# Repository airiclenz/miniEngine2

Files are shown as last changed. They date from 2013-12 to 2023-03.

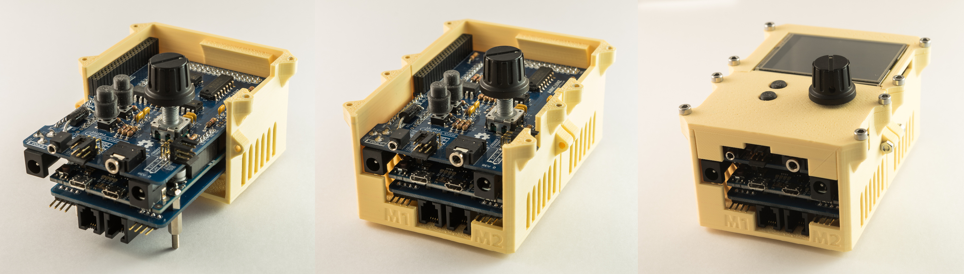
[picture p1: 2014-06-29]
Enclosures/3D Printing/Airic Lenz/miniE_case_assembly_steps.jpg

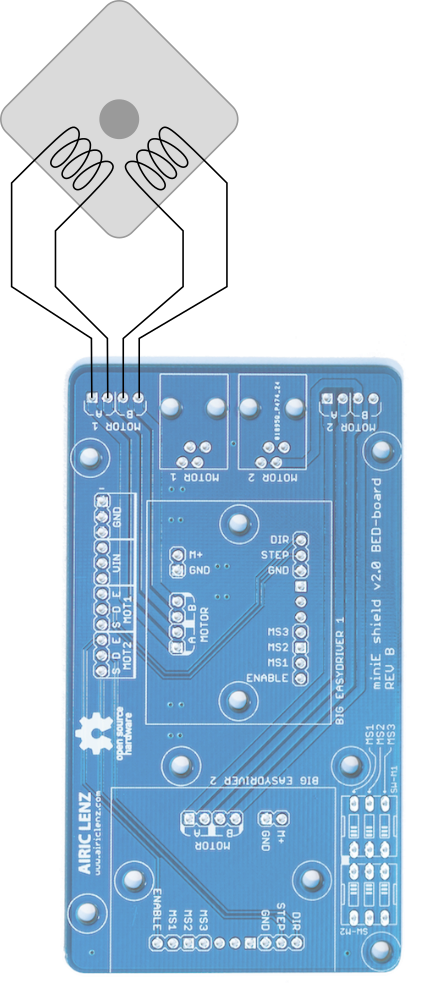
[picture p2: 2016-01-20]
Documentation/steppermotor connection.png

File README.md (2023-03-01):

miniEngine 2
============

An Arduino based multi-axis-motion-control system for time-lapse and video photogtaphy.

This repository contains all that is needed to build a full miniEngine 2 system. It contains:

	- Software
	- Hardware (PCB Gerber files)
	- Documentation
	- Licenses

Note of thanks
--------------

Four of the six contained software libraries were developed by me but two were not:

The library UTFT (here in version 2.0) was developed by Henning Karlsen
http://henningkarlsen.com/electronics/library.php?id=52

The DueTimer library was developed by Ivan Seidel 
https://github.com/ivanseidel/DueTimer

A big „Thank you“ to both of you for making these libraries available!

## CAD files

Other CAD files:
Enclosures/3D Printing/Airic Lenz/miniE2_Case.skp

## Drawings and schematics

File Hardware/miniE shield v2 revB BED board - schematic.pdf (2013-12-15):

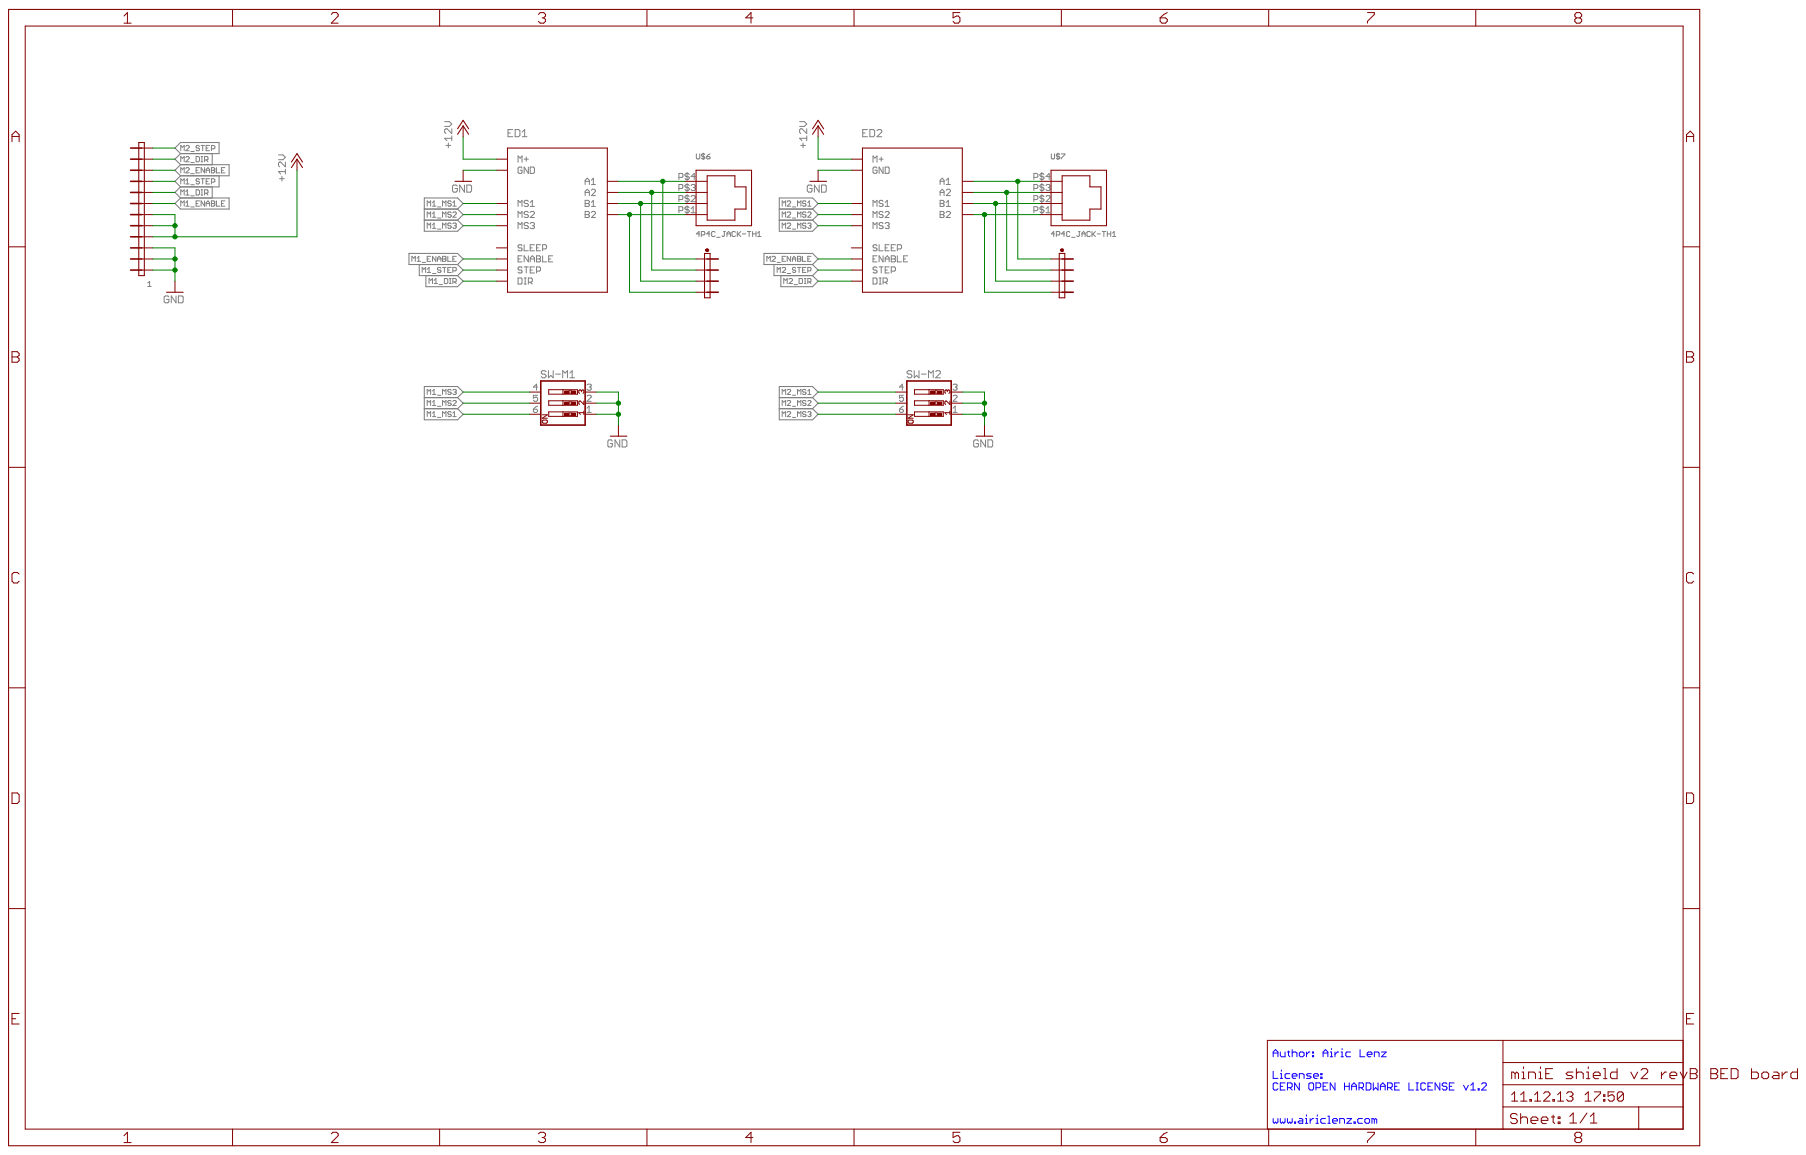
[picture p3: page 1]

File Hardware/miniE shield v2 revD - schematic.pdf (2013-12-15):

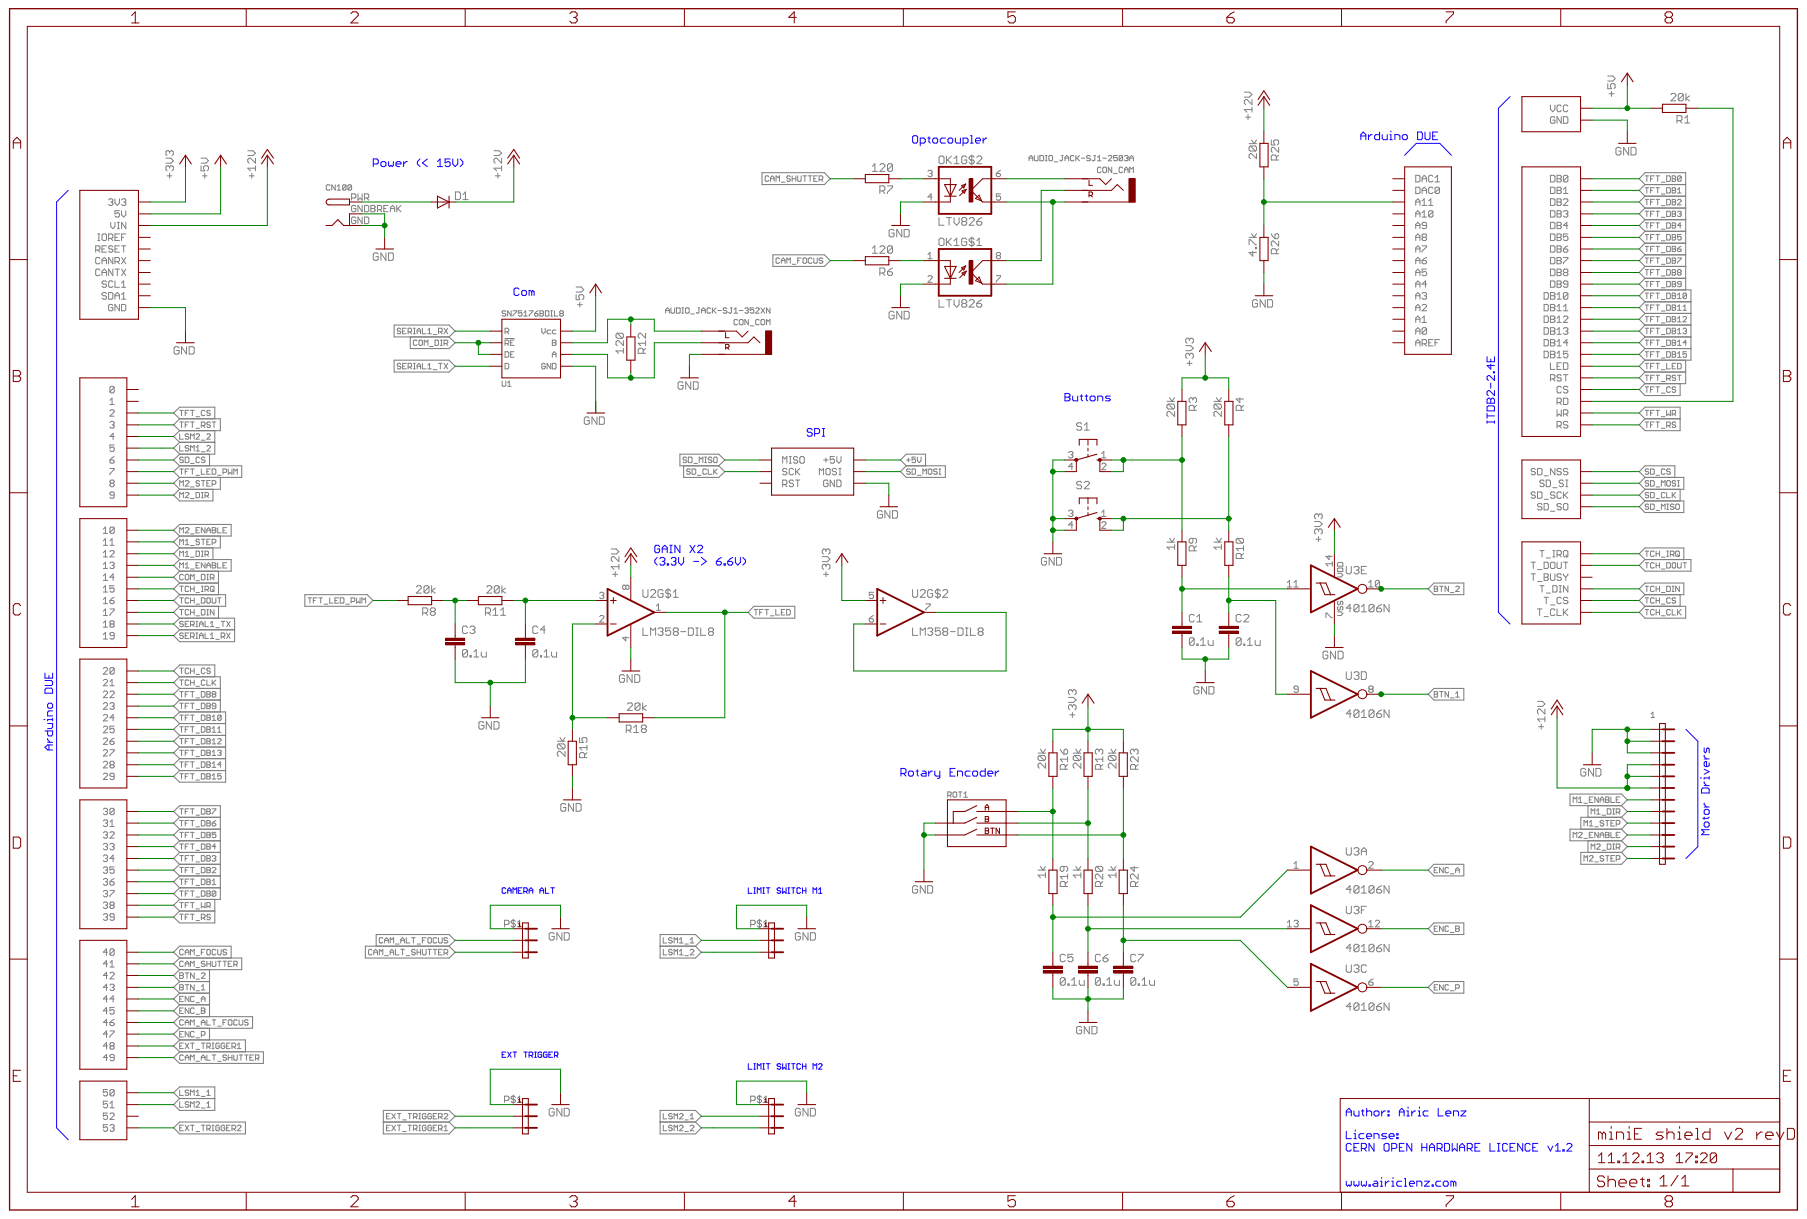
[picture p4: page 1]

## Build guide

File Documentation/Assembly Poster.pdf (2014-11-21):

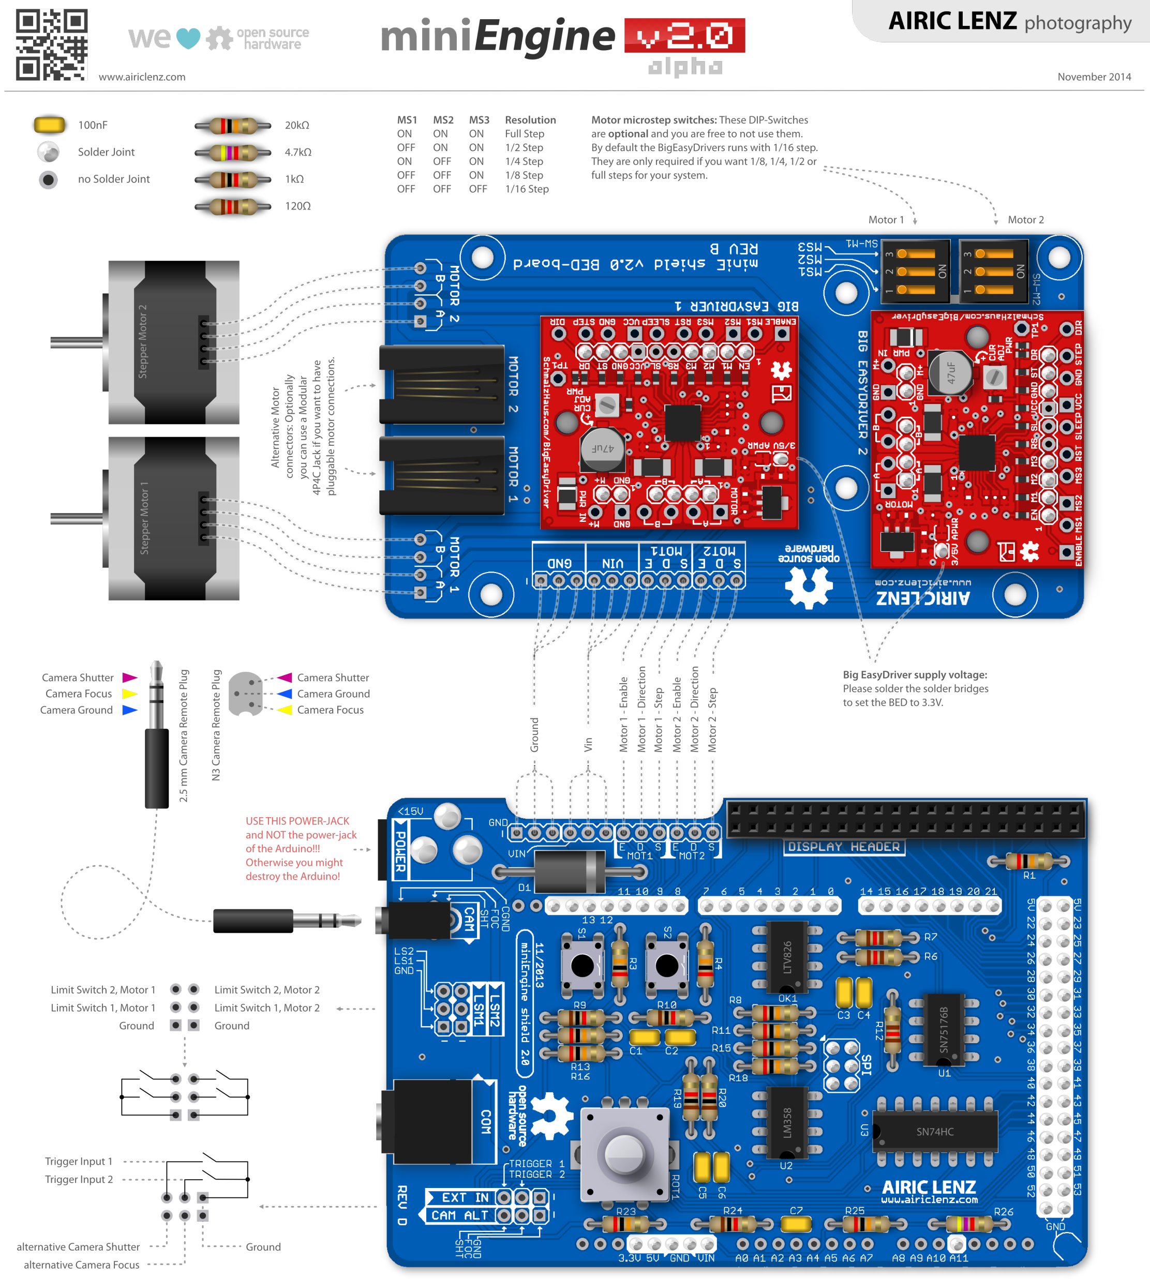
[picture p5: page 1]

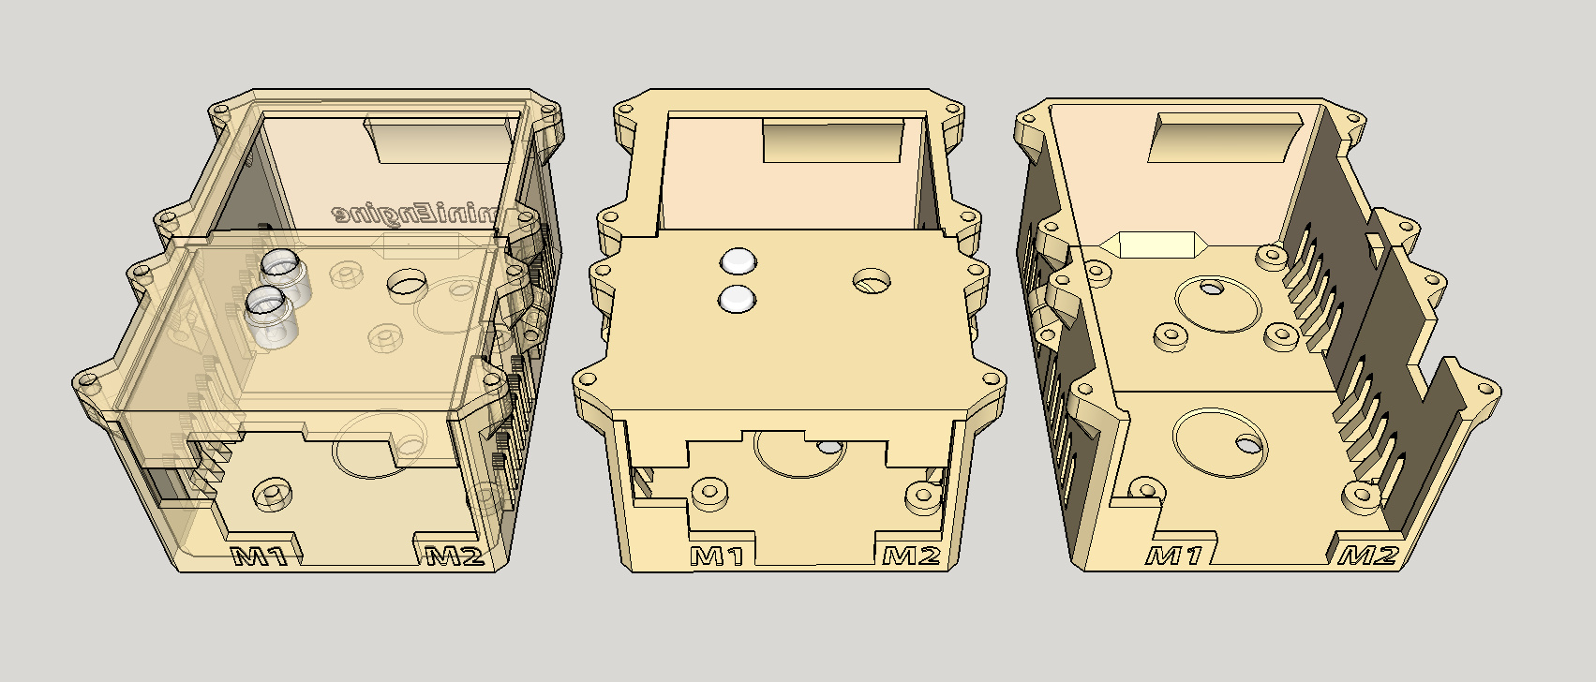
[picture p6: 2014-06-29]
Enclosures/3D Printing/Airic Lenz/miniE_case_3D.jpg

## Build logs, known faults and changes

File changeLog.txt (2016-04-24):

/////////////////////////////////////////////////////
version:	2.0.8
date:		2016-04-20

Software:

-	Added a feature to allow the camera to continue shooting
	even after the program run has ended until the user aborts
	(in Timelapse Mode)
-	Added a feature to delay the start of the motors after the
	program was started.
-	Fixed some bugs

/////////////////////////////////////////////////////
version:	2.0 alpha 7
date:		2015-07-29

Software:

-	Bouncing functionality which allows to loop the moves in 
	Video mode.
-	Multiple Language support. You can now add your own 
	language to the system. German is already included in this update.
	This feature was indroduced by Sascha Henke.
-	Added Camera Focus feature to allow a separate focus phase 
	before the exposure phase.
-	Fixed a bug that caused prevented correct saving of the 
	settings to the SD card.
-	Basic Daisy-Chaining functionality is already included but 
	not all features are in there yet.

/////////////////////////////////////////////////////
version:	2.0 alpha 6
date:		2014-06-29

Software:

-	fixed a bug that causes the initial move in SMS move to be
	wrong
-	fixed a bug in the painting routines that sometimes caused
	memory overflows
-	fixed some bugs in the core motor routines that under some conditions
	caused instable behaviour
-	added core functions for analyzing a curves max speed
-	added warning and abort if the motor-max-speed for a started
	action exceeds the defined limits
-	activating the pop-up menu now also on a menu-button long-press
-	added new pop-up menu functionalities:
	*	Set start > Defines the new start position for a move
		(equals "set home for all motors". This updates move-distance
		as well as move direction)
	*	Set End: Defines the new end position for a move
		(updates move-distance as well as move direction)
	*	Preview: Runs the timelapse setup with real-speed (total 
		preview duration = playback time) to get a feeling for the 
		planned moves. 
-	changed edit-granularity for the option "record time" 
	to 1 second for all values below 1 minute
- 	changed the FPS setting to be settable to any value between
	1 and 255
-	optimized code for ad-hoc curve generation (e.g. one move in
	SMS; move to home) for smoother moves and more consistent 
	behaviour
-	Increased Uplink functionality (for new minEngine Studio features)

Enclosures:

	- added enclosures to the resporitory

/////////////////////////////////////////////////////
version:	2.0 alpha 5
date:		2014-05-19

Documentation:

-	added a detailed assembly description for the BED
	Boards

Software:

-	added connectivity to the minEngine Studio software
	*	added new "Keyframes Mode" which is dedicated to work 
		only together with the miniEngine Studio
-	added a function that updates settings to the new version
	(no settings get lost during an update)
-	improved dashboards
-	improved settings menu-header
-	optimized system modes and run styles for easier use
-	fixed a bug where the motor was not moving when
	motor sleep was enabled
-	fixed a bug that not saved the keep powered status

/////////////////////////////////////////////////////
version:	2.0 alpha 4
date:		2014-02-19

Software:

-	added external trigger input system (starting, stopping 
	and shooting the camera)
-	added a Dashboards that is displayed when the miniEngine 
	is running
-	added a messaging system
-	added a new system font

/////////////////////////////////////////////////////
version:	2.0 alpha 3
date:		2014-01-25

Documentation:

-	updated the documentation (added small system-user-manual)
-	added some information about updating the software

Software:

-	fixed a bug which started moves from the wrong position 
	if not moved to home before
-	fixed a bug that moved the motor in the wrong direction
	when using the function "Move home (all)"
-	fixed a bug which cause the motor direction to change 
	sporadically during motor jogging
-	added a new menu font and a fon option
-	Minor user interface changes
-	added all needed libraries into the repository

/////////////////////////////////////////////////////
version:	2.0 alpha 2
date:		2013-12-18

Software:

- 	improved in-system help	to multiline text
-	fixed a motor-direction-bug in SMS mode 

/////////////////////////////////////////////////////
version:	2.0 alpha 1
date:		2013-12-17

Documentation:

-	added a motor-jack warning
- 	corrected an error with a wrong resistor-color-code 

Software:

-	added motor home functions to the pop-up menu
-	added action-menu-point functionalities
- 	implemented an intital simple help system 

/////////////////////////////////////////////////////
version:	2.0 alpha 0
date:		2013-12-15

- initial realease of the miniEngine v2 (still in alpha)

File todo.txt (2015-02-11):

TODO For v2 alpha 7
===================

-	daisy chaining
-	bouncing
-	language
-	focus time

TODO New Functionalities / IDEAS
================================

- 	check limit switch sensitivity
- 	add "Bouncing" functionality
- 	make keyframes from the minEngine Studio savable on the miniEngine
- 	add "About" screen
-   bulb ramping
-   park position for transport
-   names for axes (instead of motor 1, motor 2, ...)
-   changable limit switch retract amount
-   all axes joystick
-   panorama mode

TODO Bugs
=========

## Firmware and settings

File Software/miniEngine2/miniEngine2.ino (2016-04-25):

/*

    Author: Airic Lenz, C.A. Church
    Year of release: 2016
    
    See www.airiclenz.com for more information

    The 1st version of this code, dealing with core functionalities, 
    was heavily inspired by the OpenMoCo Engine by C.A. Church
    and is basically based on it. Thank you for your great work! 
        
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
*/


#ifdef __arm__
  #include "itoa.h"
#endif

#include <SPI.h>
#include <SD.h>

#include <UTFT.h>
#include <RotaryEncoder.h>
#include <StepperMotor.h>
#include <MoCoM.h>
#include <bitOps.h>
#include <DueTimer.h>

// free mem stuff
#include <malloc.h>
#include <stdlib.h>
#include <stdio.h>

extern char _end;
extern "C" char *sbrk(int i);
char *ramstart=(char *)0x20070000;
char *ramend=(char *)0x20088000;



// some replacements for fast coding
//#define   prn   Serial.print
//#define   prnl  Serial.println



////////////////////////////////////////////////////////
//                                                    //
//  L A N G U A G E                                   //
//                                                    //
////////////////////////////////////////////////////////

#define LANGUANGE_ENGLISH
//#define LANGUANGE_GERMAN
//#define LANGUANGE_ITALIAN


////////////////////////////////////////////////////////
//                                                    //
//  D I S P L A Y   T Y P E                           //
//                                                    //
////////////////////////////////////////////////////////


// if you have an older version of the display, use
// this line of code (if you get a white screen with
// this one, change to the other display type):
#define DISPLAY_TYPE        ITDB24E_16    

// if you have a newer version of the display or you get a
// white screen, use one of these lines of code 
// (remove the "//" and add it to the above definition):

//#define DISPLAY_TYPE        TFT01_24_16
//#define DISPLAY_TYPE        S6D1121_16
//#define DISPLAY_TYPE        ILI9325D_16
//#define DISPLAY_TYPE        ILI9325D_16ALT



////////////////////////////////////////////////////////
//                                                    //
//  V E R S I O N                                     //
//                                                    //
////////////////////////////////////////////////////////


#define VERSION                      2
#define SUBVERSION                   0  
#define SUBSUBVERSION                8

const char* STR_VER                  = "beta";


////////////////////////////////////////////////////////
//                                                    //
//  F O N T S                                         //
//                                                    //
////////////////////////////////////////////////////////


extern uint8_t smallMax[];
extern uint8_t mE_Clear[];
extern uint8_t Sinclair_M[];
extern uint8_t Arial[];


////////////////////////////////////////////////////////
//                                                    //
//  P I N   D E F I N I T I O N S                     //
//                                                    //
////////////////////////////////////////////////////////

#define PIN_BACKLIGHT                7

#define PIN_ROTARY_A                 44
#define PIN_ROTARY_B                 45
#define PIN_ROTARY_PRESS             47


#define PIN_TOUCH_CLK                21
#define PIN_TOUCH_CS                 20
#define PIN_TOUCH_DIN                17
#define PIN_TOUCH_DOUT               16
#define PIN_TOUCH_IRQ                15

#define PIN_TFT_RS                   39 
#define PIN_TFT_WR                   38
#define PIN_TFT_CS                   2 
#define PIN_TFT_RST                  3

#define PIN_KEY_1                    43
#define PIN_KEY_2                    42

#define PIN_CAM_SHUTTER              41
#define PIN_CAM_FOCUS                40
#define PIN_CAM_ALT_SHUTTER          49 
#define PIN_CAM_ALT_FOCUS            46 

#define PIN_MOTOR1_STEP              11 
#define PIN_MOTOR1_DIR               12
#define PIN_MOTOR1_ENABLE            13
#define PIN_MOTOR1_LS1               50 
#define PIN_MOTOR1_LS2               5 

#define PIN_MOTOR2_STEP              8 
#define PIN_MOTOR2_DIR               9
#define PIN_MOTOR2_ENABLE            10
#define PIN_MOTOR2_LS1               51 
#define PIN_MOTOR2_LS2               4


#define PIN_TRIGGER1                 48 
#define PIN_TRIGGER2                 53


#define PIN_BATTERY                  A11        

#define PIN_COM_DIR                  14  

#define PIN_SD_SS                    6


////////////////////////////////////////////////////////
//                                                    //
//  O T H E R   D E F I N I T I O N S                 //
//                                                    //
////////////////////////////////////////////////////////


#define DEF_MOTOR_COUNT                      2


#define  MILLIS_PER_SECOND                1000
#define  MILLIS_PER_MINUTE               60000
#define  MILLIS_PER_HOUR               3600000
#define  MILLIS_PER_DAY               86400000

#define  BYTE_MAX                          255
#define  UINT_MAX                        65535
#define  ULONG_MAX                  4294967295


// time delay after pressing the start button to allow 
// the system to settle down after pressing activating the motors
#define  SYSTEM_START_DELAY              1500L        


////////////////////////////////////////////////////////
//                                                    //
//  S Y S T E M   M O D E S                           //
//                                                    //
////////////////////////////////////////////////////////



// System Modes
#define  MODE_COUNT              3
#define  MODE_TIMELAPSE          B00000001
#define  MODE_VIDEO              B00000010    
#define  MODE_PANORAMA           B00000100    

// setup styles
#define  SETUP_STYLE_COUNT       3
#define  SETUP_STYLE_RUN         B00000001
#define  SETUP_STYLE_KEYFRAMES   B00000010
#define  SETUP_STYLE_REMOTE      B00000100

// move styles
#define  MOVE_STYLE_COUNT        2
#define  MOVE_STYLE_SMS          B00000001    
#define  MOVE_STYLE_CONTINUOUS   B00000010    



uint8_t core_mode         = MODE_TIMELAPSE;
uint8_t core_setup_style  = SETUP_STYLE_RUN;
uint8_t core_move_style   = MOVE_STYLE_SMS;




////////////////////////////////////////////////////////
//                                                    //
//  K E Y F R A M E   C U R V E S                     //
//                                                    //
////////////////////////////////////////////////////////


// the structure used for storing the curve data
typedef struct motorCurve {
  MotorBezier      curve;
  QuadBezierCurve  curveDefinition;
  uint8_t          used;
  
};


// Kurves for keyframes:
// every curve has 200 segments (which consist of 12 byte each) and 9 bytes other stuff
// variables: 
// --> (200 * 12 byte) + 13 bytes = 2413 byte
// --> 2413 byte * 25 = 60325 byte of RAM
#define CURVE_COUNT  25
struct motorCurve mCurves[CURVE_COUNT];
// curves for on demand moves like in SMS or Motor go home:
// --> 2 more curves in the RAM: 60325 byte + (2 * 2413 byte) = 65151 bytes
MotorBezier tempCurves[DEF_MOTOR_COUNT];



////////////////////////////////////////////////////////
//                                                    //
//  G L O B A L   V A R I A B L E S   &   D E F S     //
//                                                    //
////////////////////////////////////////////////////////



// a global variable for the current "time" in milliseconds since the CPU
// was powered up. This is to be used for non-precision events like the 
// display backlight
uint32_t now;


// key codes
#define  KEY_NONE                  B00000000
#define  KEY_ROTARY                B00000001
#define  KEY_1                     B00000010
#define  KEY_UP                    B00000100
#define  KEY_DOWN                  B00001000
#define  KEY_2                     B00010000

#define  KEY_2_LONG                B00100000
#define  KEY_ROTARY_LONG           B01000000


////////////////////////////////////////////////////////
//                                                    //
//  P R O G R A M   V A R A B L E S                   //
//                                                    //
////////////////////////////////////////////////////////



// B0 = camera phase
// B1 = motor phase
// B2 = motor post delay phase
// B3 = 
// B4 = 
// B5 = 
// B6 = 
// B7 = 
uint8_t system_phase = 0;



// a variable to remember when a system phase started;
uint32_t system_cycle_start;

// interval warning (actions during cycle longer than defined cycle)
bool system_cycle_too_long = false;


uint8_t   setup_run_ramp_out[DEF_MOTOR_COUNT]     = { 0  , 0   };
uint8_t   setup_run_ramp_in[DEF_MOTOR_COUNT]      = { 0  , 0   };
uint8_t   setup_run_move_delay[DEF_MOTOR_COUNT]   = { 0  , 0   };


uint8_t   cam_fps               = 25;
uint32_t  cam_exposure          = 100;
uint32_t  cam_focus             = 0;
uint32_t  cam_post_delay        = 200;

uint32_t  setup_record_time     = 15 * MILLIS_PER_MINUTE;  // 15 minutes
uint32_t  setup_play_time       = 12 * MILLIS_PER_SECOND;  // 12 seconds

// the amount of photos we need to make during the run
int16_t   setup_frame_count     = cam_fps * (setup_play_time / 1000.0); 
uint32_t  setup_interval_length = setup_record_time / (setup_frame_count - 1);


float     motor_total_distance[DEF_MOTOR_COUNT] = { 0.0, 0.0 };

uint32_t  core_program_start_time;

// panorma variables
uint8_t   panorama_pics_m1      = 10;
uint8_t   panorama_pics_m2      = 5;
uint8_t   panorama_pos_m1       = 0;
uint8_t   panorama_pos_m2       = 0;


////////////////////////////////////////////////////////
//                                                    //
//  G L O B A L   O B J E C T S                       //
//                                                    //
////////////////////////////////////////////////////////


// RotaryEncoder:
RotaryEncoder rotary(PIN_ROTARY_A, PIN_ROTARY_B);

// StepperMotor:
StepperMotor motors[DEF_MOTOR_COUNT] = { StepperMotor(PIN_MOTOR1_STEP, PIN_MOTOR1_DIR),
                                         StepperMotor(PIN_MOTOR2_STEP, PIN_MOTOR2_DIR)
                                       };

// COM (for daisy chaingin):
MoCoM com(PIN_COM_DIR, Serial1);


// Display:   
UTFT tft(DISPLAY_TYPE, PIN_TFT_RS, 
                       PIN_TFT_WR, 
                       PIN_TFT_CS, 
                       PIN_TFT_RST);




// ============================================================================
// ============================================================================
// ============================================================================
void setup() {
  
  // used for uplink functionality (miniEngine Studio)
  Serial.begin(19200);
  
  // randomize
  uint16_t a0 = analogRead(A0);
  uint16_t a4 = analogRead(A4);
  uint16_t a7 = analogRead(A7);
  randomSeed((a0 |= a7) &= ~a7);
  
  
  // initialize all components
  core_init();
  uicore_init();
  motor_init();
  input_init();
  com_init();
  cam_init();
  trigger_init();
  //touch_init();
  
    
  //printFreeRam();
  
  
  // paint the splashscreen  
  uipaint_splashScreen();  
  // clear the screen
  tft.clrScr();
  
  
  sd_init();  // also loads the settings
  power_init();
 
  
  // check if all values are calculated correctly after loading
  // the settings from the SD card
  core_checkValues();
  
  
  // do a full repaint
  uicore_repaint(true);
  // enable the backlight
  uicore_setBacklight(true);
  // clear all input events that might have happened so far
  input_clearKeyEvent();
  
  
}




// ============================================================================
// ============================================================================
// ============================================================================
void loop() {
  
  // for avoiding the overhead of leaving the loop function and then 
  // entering it again, we just use an eternal loop
  while(1) {
    
    // what time is it?
    now = millis();
    
    // process the different parts of the software
    input_process();
    uicore_process();
    power_process();
    motor_process();
    com_process();
    cam_process();
    sd_process();
    trigger_process();
    uplink_process();
       
    
    //////////////////////////////////
    if (core_isProgramRunningFlag()) {
      
      // did we just start? If yes remeber some times
      core_checkIfStarted();
      
      ////////////////////////////
      // T I M E L A P S E
      if (isBit(core_mode, MODE_TIMELAPSE)) {
      
        ////////////////////////////
        // did the next cycle start?    
         if (
             (system_phase == 0) &&
             core_isNextCycle()) {
               
          // when did this cycle start?   
          system_cycle_start = millis();   
              
          // set the system status to the camera-phase
          system_phase = BIT_0;    
          
          // trigger the camera  
          cam_start();
                      
        } // end: the next cycle started
        
       
        ////////////////////////////   
        // camera phase
        if (isBit(system_phase, BIT_0)) {
          
          // is the camer phase over?
          if (!cam_isCameraWorking()) {
            
            // check if the program is done
            core_checkIfTimelapseDone();
            
            // if we are in a curve-based-move mode, just go back to
            // the cycle start
            if (isBit(core_move_style, MOVE_STYLE_CONTINUOUS)) {
              
              // reset the system phase flag and thus restart the cycle
              system_phase = 0;
                          
              // check if we need tp print a warning sign
              core_checkIfCycleWasToLong();
              
            } 
            
            // if we are in SMS mode, do the motor move stuff now
            else {
              
              // go to the post delay phase 
              // (shift the phase bit one position to the left)
              system_phase = system_phase << 1;
              
              // initiate the motor stuff
              motor_startMotorPhase();
              
            }
             
          } // end: camera is done
           
        } // end: camera phase ended
         
         
         
        ////////////////////////////
        // motor phase
        if (isBit(system_phase, BIT_1)) {
           
          // check if the motor moves are done
          if (!motor_isMoveToPositionRunning()) {
            
            // go to the motor post phase
            system_phase = system_phase << 1;
            
          } 
           
        } // end: motor phase
         
         
        ////////////////////////////
        // motor post delay
        if (isBit(system_phase, BIT_2)) {
         
          // when the motor post delay ended
          if (!motor_isPostDelay()) {
            
            // checks and sets the sleep function if needed          
            motor_startSleep();
            
            // reset the system phase flag and thus restart the cycle
            system_phase = 0;
            
            // check if we need tp print a warning sign
            core_checkIfCycleWasToLong();
            
          
          } // end: motor post delay ended
         
        } // end: motor post delay phase
                    
      } // end: Timelapse mode            
             




             
      ////////////////////////////
      // V I D E O
      else if (isBit(core_mode, MODE_VIDEO)) {      
        
        // if the program time is over
        if (core_checkIfVideoDone()) {
          
          // are we in bouncing mode?
          if (core_isLoopFlag()) {
            
            // this markes if the following move is backwards or not
            // if this flag is set, the move will be inverted
            core_toggleLoopedMoveFlag();
            
            // invert all the curves
            motor_invertCurves();
            
            // if we are a master, wait a little bit to have all clients
            // finalized their moves (crystals are not running 
            // at 100% the same speed ;) 
            if (com.isMaster() && (com.getSlaveCount() > 0)) core_delay(500);
            
            // start the new move
            motor_startContinuousMove();
            // set the flag indicating that we just started with a new move
            core_setProgramStartedFlag();
            
          } else {
            
            // stop the program
            core_stopProgram(com.isMaster() && (com.getSlaveCount() > 0));
            
          }
          
        } // end: is program over? 
        
      } // end: is video mode? 







      ////////////////////////////
      // P A N O R A M A
      else if (isBit(core_mode, MODE_PANORAMA)) {      

        ////////////////////////////
        // are we ready for the next picture? (camera phase)
        if (system_phase == 0)
        {
          
          // when did this cycle start?   
          system_cycle_start = millis();   
              
          // set the system status to the camera-phase
          system_phase = BIT_0; // Bx00000001   
          
          // trigger the camera  
          cam_start();
          
        } // end: start phase

        
        ////////////////////////////   
        // camera phase
        if (isBit(system_phase, BIT_0)) {
          
          // is the camer phase over?
          if (!cam_isCameraWorking()) {

            // move to the motor phase
            system_phase = BIT_1; // Bx00000010

            // caluclate the new position for motor 1
            float newPos = (motor_total_distance[0] / (float) panorama_pics_m1) * (float) panorama_pos_m1;
            // define a move to the next position for motor 1;
            motor_defineMoveToPosition(0, newPos, true);
              
            // caluclate the new position for motor 1
            newPos = (motor_total_distance[1] / (float) panorama_pics_m2) * (float) panorama_pos_m2;
            // define a move to the next position for motor 2;
            motor_defineMoveToPosition(1, newPos, true);

            
            // calculate the next motor positions
            if (panorama_pos_m1 < panorama_pics_m1)
            {
              panorama_pos_m1++;
            }
            else
            {
              panorama_pos_m1 = 0;

              if (panorama_pos_m2 == panorama_pics_m2)
              {
                // stop the program - all done
                core_stopProgram(true);
              }
              
              if (panorama_pos_m2 < panorama_pics_m2)
              {
                panorama_pos_m2++;
              }
                            
            }
            
            // start moving to the next pos;
            motor_startMovesToPosition();
              
          } // end: camera phase is over
        
        } // end: camera phase


        ////////////////////////////
        // motor phase
        if (system_phase == BIT_1) {
           
          // check if the motor moves are done
          if (!motor_isMoveToPositionRunning()) {

            // go to the motor post phase
            system_phase = BIT_2; // Bx00000100
            
          } 
           
        } // end: stop motor phase


        ////////////////////////////
        // motor post delay
        if (system_phase == BIT_2) {
         
          // when the motor post delay ended
          if (!motor_isPostDelay()) {
            
            // checks and sets the sleep function if needed          
            motor_startSleep();
            
            // reset the system phase flag and thus restart the cycle for the next picture
            system_phase = 0;
          
          } // end: motor post delay ended
         
        } // end: motor post delay phase

      } // end: panorama mode?


                     
    } // end: program is running
        
  } // end: while 1 inner eternal loop
    
} // end: function loop









// ============================================================================
void printFreeRam() {

  char *heapend=sbrk(0);
  register char * stack_ptr asm ("sp");
  struct mallinfo mi=mallinfo();

  Serial.println();
  Serial.println();
  Serial.println();
  
  Serial.print(F("Dynamic ram used: ...... "));
  Serial.print(mi.uordblks);
  Serial.println(F(" bytes"));
  
  Serial.print(F("Program static ram used: "));
  Serial.print(&_end - ramstart); 
  Serial.println(F(" bytes"));
  
  Serial.print(F("Stack ram used: ........ "));
  Serial.print(ramend - stack_ptr);
  Serial.println(F(" bytes")); 
 
  Serial.print(F("~ Free mem: ............ "));
  Serial.print(stack_ptr - heapend + mi.fordblks);
  Serial.println(F(" bytes"));
  
  Serial.println();
  Serial.println();
}

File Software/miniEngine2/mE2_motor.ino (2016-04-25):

/*

    Author: Airic Lenz
    Year of release: 2016

    See www.airiclenz.com for more information
        
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
*/

#define TIMER_PERIOD            100         // call the timers every X microseconds 
#define DEF_LS_DEBOUNCE         50          // ms debounce for limit switches
#define DEF_MIN_POS_ERROR       0.000001    // unit: cm/°; used for accuracy check of float variables


#define MOVE_MODE_NONE          0           // this motor is not supposed to move
#define MOVE_MODE_TO_POS	      BIT_1       // this motors is using the temp curves for individual moved
#define MOVE_MODE_CURVE         BIT_2       // this motor is doing long moves with multiple curves



// B0 = limit switch - motor 1 - switch 1
// B1 = limit switch - motor 1 - switch 2
// B2 = limit switch - motor 2 - switch 1
// B3 = limit switch - motor 2 - switch 2
// B4 = 
// B5 = 
// B6 = 
// B7 =  
volatile uint8_t motor_ls_status = 0;


// variables used for soft-debouncing of the limit switches
volatile uint32_t lsm11_time,
                  lsm12_time,
                  lsm21_time,
                  lsm22_time;



// B0 = Jog timer running (Timer 1)
// B1 = Jog timer processing (semaphore)
// B2 = Move timer running (Timer 2)
// B3 = Move timer processing (sempahore) 
// B4 = 
// B5 = 
// B6 = 
// B7 =  
volatile uint8_t motor_timer_status = 0;


// B0 = store the move-start time for motor 0
// B1 = store the move-start time for motor 1
// B2 = store the move-start time for motor 2 (unused in this version)
// B3 = store the move-start time for motor 3 (unused in this version)
// B4 = ...
// B5 = 
// B6 = 
// B7 = 
volatile uint8_t motor_time_status = 0;


// B0 = motor-post is active for motor 0
// B1 = motor-post is active for motor 1
// B2 = motor-post is active for motor 2 (unused in this version)
// B3 = motor-post is active for motor 3 (unused in this version)
// B4 = ...
// B5 = 
// B6 = 
// B7 = 
volatile uint8_t motor_post_delay_status = 0;




// the currently selected motor
byte motor_selected = 0;

// the global motor factor for speeding up moves
volatile float motor_time_factor;

// the time used for ramping into- and out of moves (longer = smoother) 
float motor_ramp_time[DEF_MOTOR_COUNT];
 
// turn off the motor after moving
float motor_sleep[DEF_MOTOR_COUNT]; 

// defines the actual method hwo the motor needs to be moved
// >> SMS or Continuous (=Video)
volatile uint8_t motor_move_mode[DEF_MOTOR_COUNT];
	

// an array that stores which of the available curves are used
// by the different motors 
// dimension 1: the motor #
// dimension 2: # of the curve in the main curves array (index pointer)
volatile uint8_t motor_used_curves[DEF_MOTOR_COUNT][CURVE_COUNT];

// how many of the used-curves-array did we actually use?
// this array is used together with motor_used_curves and defines up to 
// where the stack (motor_used_curves) is filled
volatile uint8_t motor_used_curves_count[DEF_MOTOR_COUNT];

// the current curve being used (position in the motor_used_curves array)
// this little array is for running the curves
volatile uint8_t motor_used_curves_index[DEF_MOTOR_COUNT];


// some variables to track the motor direction during moves
//boolean motor_dir, motor2_dir, motor1_dir_old, motor2_dir_old;
//volatile bool  motor_dir[DEF_MOTOR_COUNT];
//volatile bool  motor_dir_old[DEF_MOTOR_COUNT];

// the direction the motor should use in the program
volatile bool  motor_program_direction[DEF_MOTOR_COUNT];

// when whas a motor move started? (in seconds)
volatile float motor_start_time[DEF_MOTOR_COUNT];

// when whas a motor post started? (in system milliseconds)
volatile uint32_t motor_post_start_time[DEF_MOTOR_COUNT];

// where was the motor when the program was started?
volatile float  motor_reference_pos[DEF_MOTOR_COUNT] = { 0.0, 0.0 };

// when whas a motor move started? (in seconds)
boolean motor_check_speed[DEF_MOTOR_COUNT];


// used timers for checking if the motors need to move.
// When running a timer is called 20000 times per second.
//#define timer_move    Timer0    // --> All curve based motor moves
//#define timer_jog     Timer1    // --> Jogging

DueTimer timer_move(0);  // --> All curve based motor moves
DueTimer timer_jog(1);   // --> Jogging




// ============================================================================
float motor_getTimeFactor() { return motor_time_factor; }


// ============================================================================
// Motor initialization
// ============================================================================
void motor_init() {
	
  // set the limit switch pins as input
  pinMode(PIN_MOTOR1_LS1, INPUT);
  pinMode(PIN_MOTOR1_LS2, INPUT);
  pinMode(PIN_MOTOR2_LS1, INPUT);
  pinMode(PIN_MOTOR2_LS2, INPUT);

  // enable the internal pull-ups
  digitalWrite(PIN_MOTOR1_LS1, HIGH);
  digitalWrite(PIN_MOTOR1_LS2, HIGH);
  digitalWrite(PIN_MOTOR2_LS1, HIGH);
  digitalWrite(PIN_MOTOR2_LS2, HIGH);
  
  // init the motor ENABLE pins with the state in which the motor is ENABLED
  motors[0].setPinEnable(PIN_MOTOR1_ENABLE, LOW);
  motors[1].setPinEnable(PIN_MOTOR2_ENABLE, LOW);
	
  // attach all the motor-limit-switch interrupts with the state
  // in which they are active
  motor_attachLimitSwitchInterrupts(LOW);
  
  // attach the interrupt function to the jog timer
  timer_jog.attachInterrupt(motor_handleJog);
  // attach the interrupt function to the general motor timer
  timer_move.attachInterrupt(motor_handleMove);
  
  // the time factor to real-time
  motor_time_factor = 1.0;
	

  /////////////////////////////
  // initialize all motor curves
  for (int i=0; i<CURVE_COUNT; i++) {
    mCurves[i].used = false;
  }

  /////////////////////////////
  // initialize all motors with standard values
  for (int i=0; i<DEF_MOTOR_COUNT; i++) {
  
    // motor ramp time
    motor_ramp_time[i] = 0.5;
    
    // motor calibration
    motors[i].setCalibration(500);
    
    // motor max speed
    motors[i].setMaxSpeed(20);
    
    // motor sleep
    motor_sleep[i] = false;
    
    // motor move modes
    motor_move_mode[i] = MOVE_MODE_NONE;
    
    // how much curves do we use at the moment? None.
    motor_used_curves_count[i] = 0;
    
    // reset the index in the array to the first position 
    motor_used_curves_index[i] = 0;  
    
    // One curve is always used as we need it to define even the
    // simplet move --> assign an unused curve
    motor_assignNewCurve(i);
          
    // reset the motor move-start times
    motor_start_time[i] = 0;
    
    // enable checking the max speed
    motor_check_speed[i] = true;
    
    
    // direction variables  
    //motor_dir[i] = motors[i].getDirection();  
    //motor_dir_old[i] = motors[i].getDirection();  
  
    // reset the limit switches
    motors[i].resetLimitSwitch();
  }
	
}
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

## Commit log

2013-12-14 Commit of License and Assembly Poster
2013-12-17 Added power jack warning to the documentation
2013-12-18 Bugfix
    Fixed a motor direction bug in SMS mode
    [mE2_motor.ino, mE2_uicore.ino]
2014-06-27 preliminary work on the release 2 beta 6
    fixed a memory leak;
    changed FPS to granularity 1;
    [mE2_core.ino, mE2_motor.ino, mE2_uicore.ino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]
2014-06-29 Release 2 beta 6
    [miniE2_Case.skp]
2015-02-15 added camera focus
2015-02-19 Added a version with german language
    I added a version with other language support. Feel free to add your
    language.
    German is now integrated.
    You can switch between german and english in the miniEngine2.ino file,
    under the point "Language".
2015-02-25 worked on the daisy chaining functionality; removed some minor bugs;
    [mE2_com.ino, mE2_core.ino, mE2_input.ino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]
2015-02-27 worked on the daisy chaining sync
2015-03-02 finalized daisy chaining sync (program start and every camera trigger signal are within 0.5 microseconds)
2015-03-03 added daisy chaining for video loop
2016-04-20 just some minor spelling corrections
    [mE2_motor.ino, mE2_uicore.ino]
2016-04-21 new feature and bugfixes
    started with panorama mode;
    some bug fixes;
    [mE2_core.ino, mE2_language.ino, mE2_motor.ino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]

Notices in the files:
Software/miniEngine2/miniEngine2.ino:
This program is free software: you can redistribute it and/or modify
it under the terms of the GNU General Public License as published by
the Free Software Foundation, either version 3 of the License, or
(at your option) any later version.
